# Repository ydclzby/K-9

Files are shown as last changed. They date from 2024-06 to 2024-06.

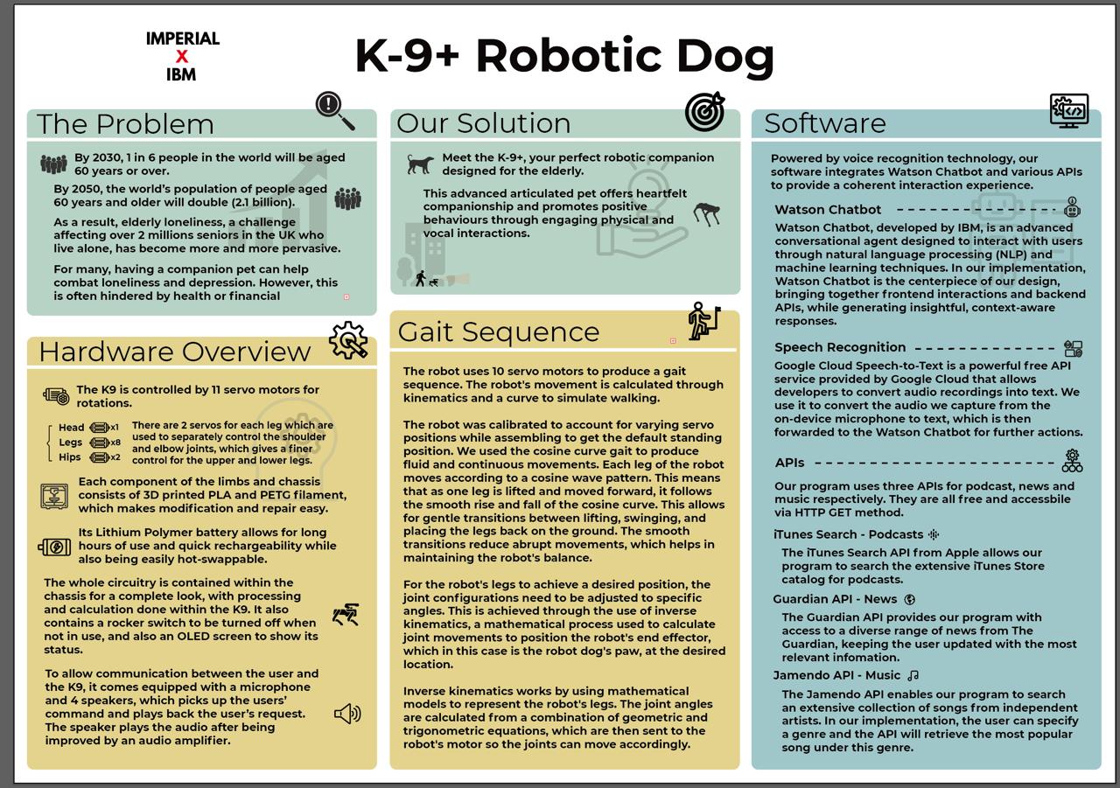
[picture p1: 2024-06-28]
Promotional Material/Poster K9.jpg

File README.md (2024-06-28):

# K-9+
Imperial team with IBM

Group Members:
- Krrish Jain
- William Ho
- Ryusei Kinosaki
- Chenglin Sun
- Boyan Zhang
- Qidong Zhou

## Introduction

The aim of this project was to build an AI companion robot pet for the elderly with the following features:

- Listen to voice commands to control the pet
- Control the movement of the pet
- Allow the pet to read the news
- Play music or podcasts requested by the user

These features help to encourage more positive behaviours for the user, through engaging physical and vocal interactions, as well as, providing companionship to help combat elderly loneliness.

### Project Manangement and Meetings

At the start of the project, there were multiple meetings to set up the necessary steps and schedule towards completion, and to give each team member a clear responsibility to contribute towards the project, which are shown [here](https://github.com/ydclzby/K-9/tree/main/Meeting%20Notes). After each part was completed and functional, it was integrated with other team member's work to create a subsystem. Each subsystem was then integrated together to create the K9, for which the team met almost every day.

## Hardware
### Components
The robodog consists of the following components:

* 11x MG995 Servo Motor
* 1x 6V, 5.5A Buck Voltage Converter
* 1x 6V to 5V/8A Buck Voltage Converter
* 1x 11.1V 3500mAh 3S1C Lithium Ion Battery
* 1x Adafruit Mini USB Microphone
* 1x MikroElektronika 2x20W Audio Amplifier
* 1x Raspberry Pi 4B (8GB RAM)
* 1x 16A Rocker Switch
* 1x OLED 128x64 Pixels
* 1x 300mm RPi Camera Ribbon
* 1x Raspberry Pi Camera
* 4x 8 Ω 1 W Speaker
* 4x Squash Balls
* PLA Filament
* PETG Filament
  
### CAD Design
The IBM K-9 bot's body is divided into 3 parts: the chassis, the legs and the head, where each of them were designed for the sake of practicality, manoeuverability and compactness.
Unless otherwise specified, the material used are PLA filament, which were 3D printed for the sake of rapid prototyping and bespoke modifications. The design was inspired by this [design](https://grabcad.com/library/quadruped-robot-w-code-1), which was shown to work consistently.

<h2>Legs</h2>
The mechanism of the legs is controlled by two servos, each controlling the shoulder (upper half of the leg) and the elbow (lower half of the leg).
The torque of the shoulder is controlled directly via the servo, whose circular attachment is slotted into the shoulder and fastened with a screw.
The torque of the elbow is transfered via the links which are attached between the servo and the elbow.
Finally, the feet of the chassis is a squash ball cut into half. The advantage of the squash ball is the higher friction surface and elasticity, preventing the K-9 from slipping while walking towards the user.

The mechanism works consistently, however, collisions and wear could loosen the joints, hence improvemets is possible with the use of ball bearings and adjusting the cad so the bearings would slot into them.

<h2>Head</h2>
The head works as a housing for the audio amplifier, speaker and the camera which could not be put into the circuit within the chassis. The design was made to be as compact as possible so that the weight would not affect the walking control. Moreover, it was made with the same design approach as the legs, where it can be easily put on the servo's circular bit.

<h2>Chassis</h2>
The chassis itself was made mainly to house the circuitry, while also holding switches and the OLED display. Instead of making one large chassis, it was divided into parts so that only one small part had to be printed in case of any problems. The central body of the chassis was made by PETG filament whose flexibility allowed for the components to be assembled easier.

### Circuitry
The circuit that controls the robodog is shown in the block diagram below. Although the battery is enough to power both the servos and the raspberry pi, when all 10 servos are used for the gait, more energy is necessary, hence requiring a power bank to power the pi. A more potent battery such as LiPo is necessary, but was not used due to budget and regulation constraints.

K9 Block

The servos were controlled by the Servo HAT to optimise space and ease of use. The raspberry cam was connected via the camera cable to the raspberry pi, and the microphone and amplifier were connected through USB and audio cable, respectively. Finally, the OLED was used to display the IP for secure shell connection.

## Software

### Chatbot

The chatbot implementation leverages IBM Watson Assistant, speech recognition, and various other APIs to provide interactive functionalities. This section details the important classes and aspects involved in the chatbot implementation.

#### SysState Class

The `SysState` class is central to managing the state of the system and coordinating interactions between the various components and APIs.

##### Initialization

- **`__init__(self, history_fp)`**
  - Initializes system state variables.
  - Sets up the IBM Watson Assistant API.
  - Configures the Picamera and servos for movement.
  - Instantiates a `Quadruped` object for controlling the robot.

##### Methods

- **chatbot_thread()**
  - Initializes the IBM Watson Assistant using the provided API key and service URL.
  - Manages a session with the Assistant, sending user commands and processing responses.
  - Adjusts the system mode based on the Assistant's responses.

- **audio_thread()**
  - Listens for audio commands using a microphone.
  - Converts speech to text using the `speech_recognition` library.
  - Sets the recognized text as a command for processing.

- **mode_thread()**
  - Executes actions based on the current mode, such as reading text, playing podcasts, fetching news, playing songs, and controlling the robot's movements.

#### IBM Watson Assistant Integration

The IBM Watson Assistant is used to interpret user commands and provide responses. 

##### Methods

- **chatbot_thread()**
  - **authenticator = IAMAuthenticator(api_key)**
    - Authenticates using the IBM Cloud API key.
  - **assistant = AssistantV2(version='2024-05-03', authenticator=authenticator)**
    - Initializes the Assistant with the specified version and authenticator.
  - **assistant.set_service_url(service_url)**
    - Sets the service URL for the Assistant.
  - **response = assistant.create_session(assistant_id=assistant_id).get_result()**
    - Creates a session with the Assistant.
  - **response = assistant.message(assistant_id=assistant_id, session_id=session_id, input=message_input).get_result()**
    - Sends user commands to the Assistant and processes the response.

#### Speech Recognition Integration

The `speech_recognition` library is used to capture and interpret audio commands from the user.

##### Methods

- **audio_thread()**
  - **recognizer = sr.Recognizer()**
    - Initializes the recognizer.
  - **mic = sr.Microphone()**
    - Sets up the microphone.
  - **audio = recognizer.listen(source, timeout=5.0, phrase_time_limit=3.0)**
    - Listens for audio input with a timeout and phrase time limit.
  - **recognized_text = recognizer.recognize_google(audio)**
    - Converts the captured audio to text using Google’s speech recognition API.

#### Additional APIs and Functionalities

##### News API

The News API fetches the latest news articles on a given topic.

- **get_news(topic)**
  - **params = {'api-key': news_api_key, 'q': topic, 'page-size': 1, 'order-by': 'relevance'}**
    - Sets the parameters for the news search.
  - **response = requests.get(news_endpoint, params=params)**
    - Sends a request to the News API to fetch articles.

##### iTunes API

The iTunes API is used to search for and play podcasts.

- **first_podcast(topic)**
  - **params = {'term': topic, 'media': 'podcast', 'limit': 1}**
    - Sets the parameters for the podcast search.
  - **response = requests.get(itunes_search_url, params=params)**
    - Sends a request to the iTunes API to search for podcasts.

##### Jamendo API

The Jamendo API fetches songs based on a given topic.

- **get_song(topic)**
  - **params = {'client_id': CLIENT_ID, 'format': 'json', 'limit': 1, 'tags': topic, 'order': 'popularity_total_desc'}**
    - Sets the parameters for the song search. This implementation fetches the most popular song under a user-specified genre (topic).
  - **response = requests.get(api_url, params=params)**
    - Sends a request to the Jamendo API to search for songs.

#### Thread Management

The chatbot employs threading to manage different tasks concurrently.

- **threading.Thread(target=ibm_Chatbot.chatbot_thread).start()**
  - Starts the chatbot thread to handle interactions with IBM Watson Assistant.
- **threading.Thread(target=ibm_Chatbot.audio_thread).start()**
  - Starts the audio thread to capture and process audio commands.
- **threading.Thread(target=ibm_Chatbot.mode_thread).start()**
  - Starts the mode thread to execute actions based on the system mode.

### Movement

For the movement, the quarduped_new.py file contains 2 classes which are responsible for controlling the robot's movements. Using the adafruit_servokit library to control the servos, the approach we chose to use was to use inverse kinematics to calculate where to position each leg.

#### Motor Class

The motor class is used to help identify the corresponding pin location with the motor location.

#### Quadruped Class

The quardruped class is the main class to control the robot. 

- The class constructor __init__, initialises the object and instantiates the ServoKit and defines the initial lengths and angles for the leg. It also sends out a pulse width range for each servo motor.
- There are 2 functions to assist with controlling the movement, set_angle, and rad_to_degree. These functions help by setting the angle for the servo and converting radians to degrees, respectively.
- The calibrate function sets the pet to it's standing up position by getting those values from a dictionary, pos_dict.
- The sit function sets the pet to a sitting position by getting the standing up position from the dictionary, pos_dict, and adjusting the shoulder values by a constant value.
- The inverse_kinematics functions runs to get the desired angles, theta1 and theta2, based on the target x and y co-ordinates.
- The move function will use the angle that is calculated in the inverse_kinematics function to set the angle of the servos to the desired positions, as well as being able to adjust the direction of movement.
- THe pushups function moves the robot to a calibrated position, lowers the back legs and then proceeds to lower and extend the front legs.
- The steps function will call on the move function based on direction for a certain number of steps.

For the inverse kinematics:
1. First calculate distance, d, as the square root of x squared + y squared
2. Then, calculate theta2, which is pi take away the arccos of the length of upper leg squared + lower leg squared - d squared divided by 2 times the lower leg length times the upper leg length.
3. Then, get phi, by getting the arccos of the upper leg squared - lower leg squared + d squared divided by 2 times the upper leg length times d squared.
4. Finally, theta1 is the arctan2 of y, x - phi.

### Computer Vision

The computer vision code is in the bone_detector.py file. This code contains one class, the Follower class, and is used to detect a green bone, the colour values are set in the variables colorLower and colorHigher. The code uses the picamera2 library for the camera and cv2 for computer vision. The code will capture array from the camera and turn it into HSV colour space which creates a mask based on the desired color ranges, noise is then removed from the mask and a moments is created of the binary mask. A rectangle is then created around the desired object and will rotate the camera to center the object and turn the robot and move towards it.

## Setup
To start up the K9, make sure that the battery is fully charged (~12.3V) and the rocker switch is set to on. Give a few minutes for the Pi to switch on, at which point the OLED at the back should show the IP when connected to the imperial network. With the K9 connected to the network, you can use your own laptop with a Linux command (Ubuntu command terminal on Windows/Mac works as well) to connect to the Pi with "sudo ssh K9@<IP>". After accepting any prompts from the terminal, you can activate the programme by running "sudo python3 chatbot_9.py", at which it can listen for commands to do whichever issues.

## Acknowledgements
We'd like to thank Jon McNamara, our company liaison, for giving us the resources and guidance with our projects. We'd also like to thank our project supervisor, Professor Pal Bikash for helping us with feedback on promotinal materials such as our leaflets.

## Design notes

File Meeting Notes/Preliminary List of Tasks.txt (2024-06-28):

- Parts list
- Order
- Software
    - Microphone
    - Chatbot API
    - Movement control
    - Face/display
    - Collision avoidance
- Hardware
    - RPi
    - Arduino
- Chassis
    - Modelling
    - 3d Print/Laser cut

## Milestone and its respective deadlines + content

1. Create subteams & organisation/roles (2nd - 7th May)
    1. Software
        1. API w/ chatbot
        2. API w/ news/music/podcast etc.
        3. Movement (Servos/Control)
        4. Computer vision
    2. Hardware
        1. Chassis
        2. Electronics
2. Create Parts list - TBD after meeting with supervisor (7th) - Deadline 10th May
3. Ordering parts - Plan to order everything by the 10th (Deliver within a week ideally)
4. Software
    1. Chatbot API with microphone on laptop (1 wk)
    2. Finding podcast & news API (1 wk)
    3. Computer vision with camera (2 wks)
5. Hardware
    1. Completing Chassis (27th May)
    2. Servo Config and control (27th May)
    3. Breadboard prototype circuit for additional sensors (20th May)
    - Possible delays from broken circuits/reprint chassis part
6. Integration (start 28th May  - 3rd June) 
    1. State machine/workflow of the bot (walking, playing music etc)
    2. Uploading different software parts on pi & debug [1 week]
    3. Movement + obstacle avoidance debugging with software/sensors [1.5 weeks]
    - In case of chassis delay - software team should start on the pi itself and integrating mic/speaker
7. Final Integration (start 13th June - 20th June)
    1. Test runs and final adjustments
    2. edge case if there is

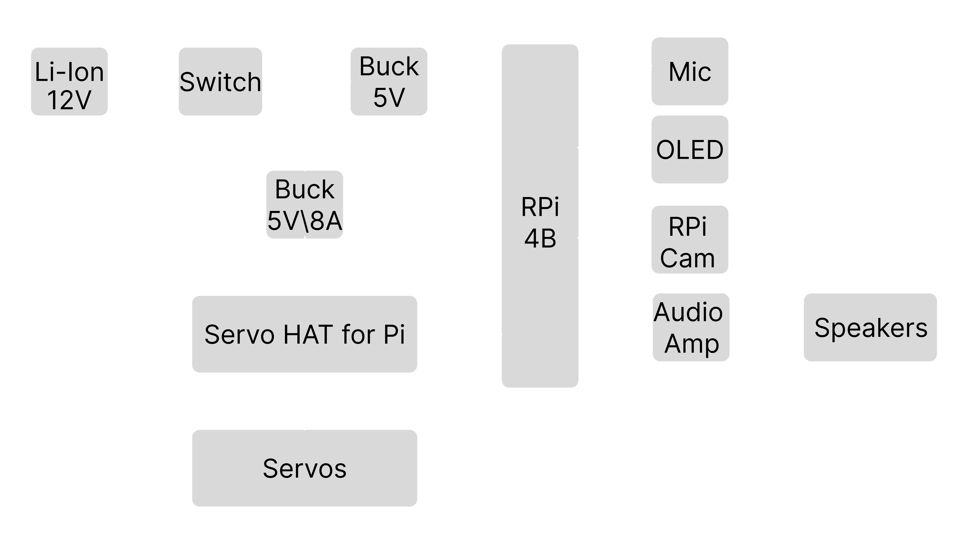
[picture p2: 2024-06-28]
images/K9 Block.png

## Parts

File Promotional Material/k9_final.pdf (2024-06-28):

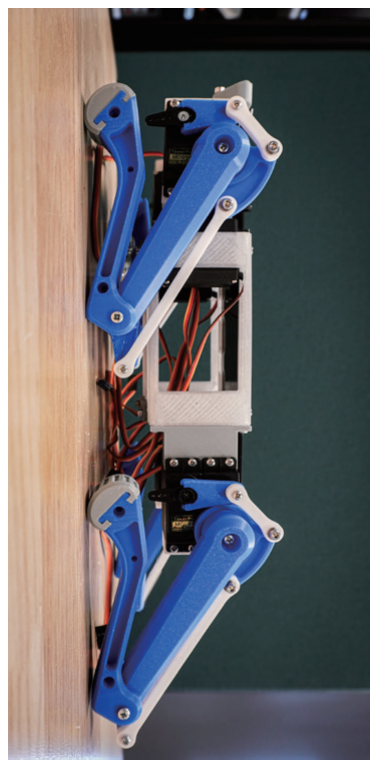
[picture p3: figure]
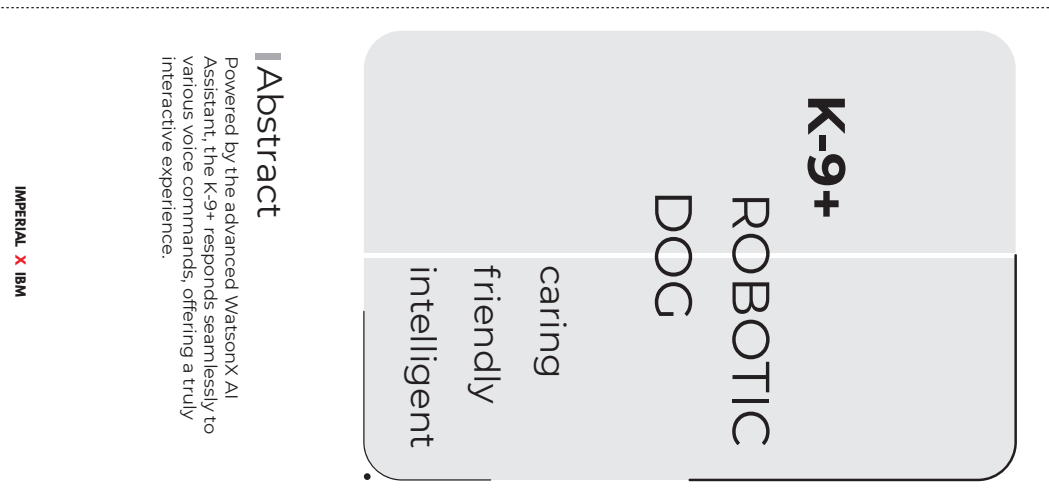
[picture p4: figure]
IMPERIAL IBM X; interactive experience.; Powered by the advanced WatsonX AI; Abstract; intelligent; friendly; caring; ROBOTIC; DOG

various voice commands, offering a truly

Assistant, the K-9+ responds seamlessly to

# Quadruped Design Hardware

navigate various terrains.

offers excellent stability, allowing it to easily

realistic movement. This advanced structure

10 degrees of freedom, enabling smooth and

The K-9+ features a quadruped design with you and motivate a healthier lifestyle.
software and computer vision, it can follow

raspberry pi running sophisticated control

natural interactions. Equipped with a

real dog, the K-9+ has lifelike movement and

# Inspired by the form and movement of a K-9+

RYUSEI KINOSAKI, QIDONG ZHOU & BOYAN ZHANG

KRRISH JAIN, WILLIAM HO, CHENGLIN SUN,

Designed by
We are a robotics technologies research

# About Us

https://github.com/ydclzby/ZMS_K9-

GitHub:

www.imperial.ac.uk

Website:

SW7 2BX

South Kensington

Imperial College London

Address:

# Contact Us

others and giving back to the society.

London Engineers with the aim of helping

group founded by six Imperial College

IMPERIAL IBM X IMPERIAL IBM X

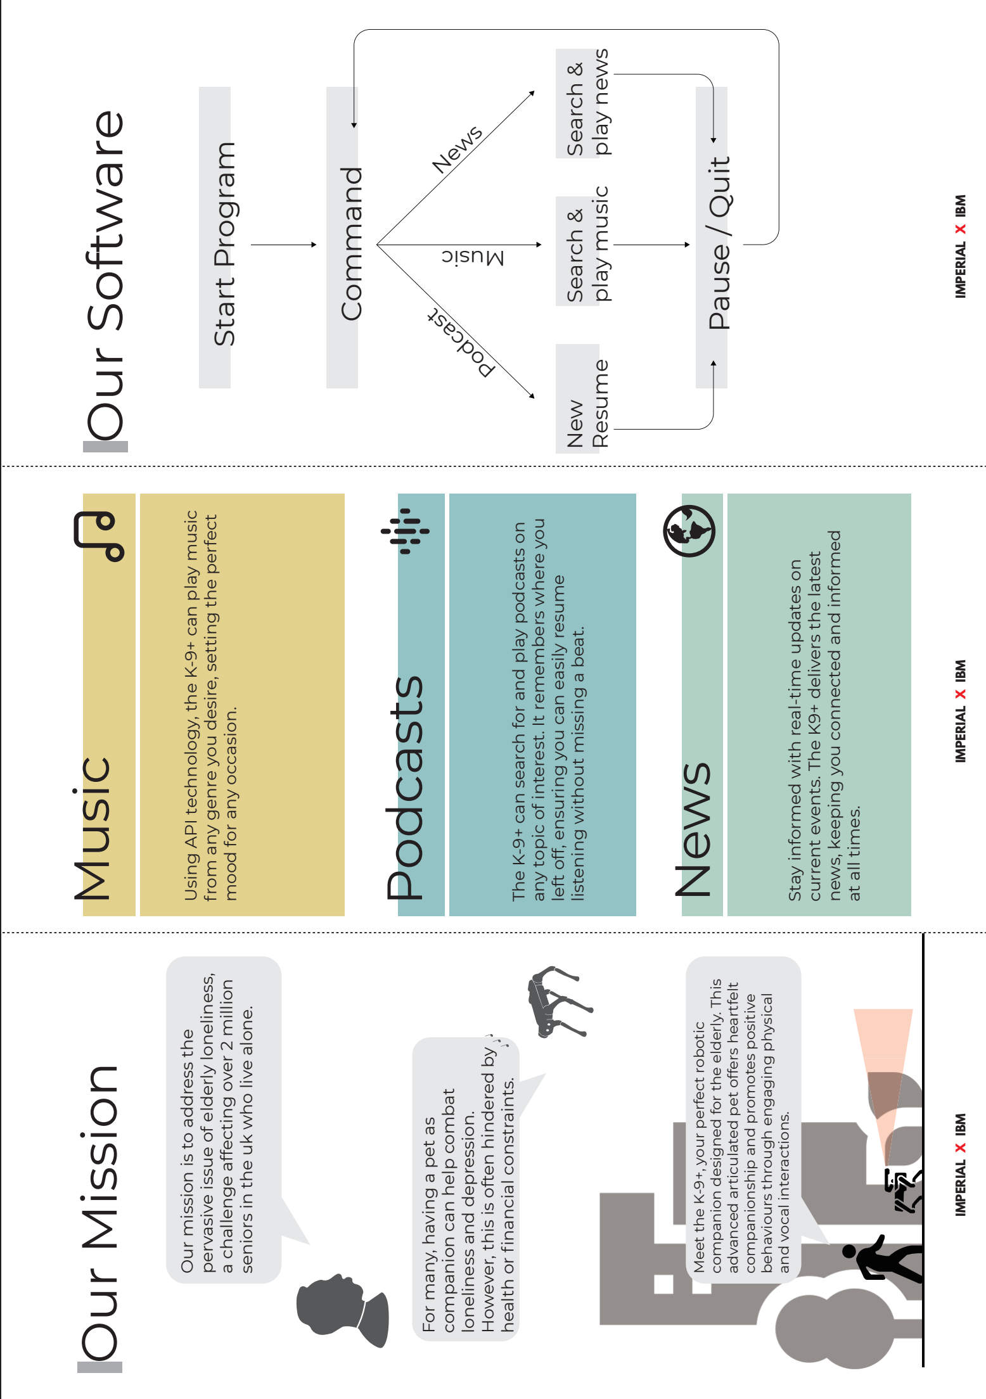
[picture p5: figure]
IMPERIAL IBM X; Our Mission Music; mood for any occasion.; Podcasts; listening without missing a beat.; News; Stay informed with real-time updates on; at all times.; Start Program; Command; Pause / Quit; New; Resume; Search &; play music; play news; Our mission is to address the; pervasive issue of elderly loneliness, a challenge affecting over 2 million seniors in the uk who live alone.; For many, having a pet as; companion can help combat loneliness and depression.; However, this is often hindered by health or financial constraints.; Meet the K-9+, your perfect robotic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

Using API technology, the K-9+ can play music
from any genre you desire, setting the perfect The K-9+ can search for and play podcasts on

any topic of interest. It remembers where you

left off, ensuring you can easily resume current events. The K9+ delivers the latest

news, keeping you connected and informed

companion designed for the elderly. This

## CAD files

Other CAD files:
CAD/Head v13.f3z
CAD/Quadruped_motor_extension_taller v3.f3d
CAD/Rear Block v12.f3d
CAD/link_belly v10.f3z

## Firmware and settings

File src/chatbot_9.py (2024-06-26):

import os 
from ibm_watson import AssistantV2
from ibm_cloud_sdk_core.get_authenticator import IAMAuthenticator
import speech_recognition as sr
import requests
import feedparser
from playsound import playsound
from urllib.parse import urlparse
from bs4 import BeautifulSoup



import threading
import vlc
import time
import json
import queue
from gtts import gTTS
from datetime import datetime
import numpy as np

# from gait_logic.quadruped import Quadruped


import cv2
from adafruit_servokit import ServoKit
from picamera2 import Picamera2
from time import sleep

from qudruped_new import Quadruped

itunes_search_url = "https://itunes.apple.com/search"

api_key = "c5fMtKdU7iDNdzmB0vIv9_t88rPExGfffuMxNCpqBQ1L"
service_url = "https://api.eu-gb.assistant.watson.cloud.ibm.com/instances/e5a41b2f-bd77-4e71-b02c-430b71625717"
assistant_id = "62222580-6d55-4e58-889f-515789eb2cd1"

news_api_key = "a0ff4132-cf60-48d7-b23f-d0523e7c67aa"
news_endpoint = "https://content.guardianapis.com/search"

threading_lock = threading.Lock()
podcast_lock = threading.Lock()
music_lock = threading.Lock()

podcast_history_fp = "../data/history/playback_history.json"

api_url = "https://api.jamendo.com/v3.0/tracks"

CLIENT_ID = 'cd92fac2'



class SysState(object):
    colorLower = (57, 100, 100)
    colorUpper = (77, 255, 255)

    HEAD_SERVO = 0
    tiltAngle = 90
    def __init__(self, history_fp):
        
        self.mode = None
        self.wait_command = True
        self.command_text = ""
        self.response = ""
        self.topic = ""
        self.control_command = "none"
        self.mic = True
        
        # Players
        self.history_fp = history_fp
        self.player = None
        self.current_start_time = None
        self.paused_arg = False
        self.quit_arg = False
        self.history_data = {}
        self.control_command = None
        self.found = True
        #self.r = Quadruped()
        
        # CV
        self.picam2 = Picamera2()
        self.picam2.configure(self.picam2.create_preview_configuration(main={"format": 'XRGB8888', "size": (640, 480)}))
        self.picam2.start()
        self.kit = ServoKit(channels=16)
        self.kit.servo[0].set_pulse_width_range(500,2500)
        self.set_servo_angle(90)
        self.tiltAngle = 90
        self.cv_switch = True
        self.centred = False
        self.r = Quadruped()
        self.r.calibrate()
        
    def set_servo_angle(self,degrees):
        self.kit.servo[0].angle = degrees

    def move_servo(self,x,y):
        if (x < 240):
            self.tiltAngle += 3
            if self.tiltAngle > 140:
                self.tiltAngle = 140
                #print("move left")
            self.set_servo_angle (self.tiltAngle)
            sleep(0.02)
        if (x > 400):
            self.tiltAngle -= 3
            if self.tiltAngle < 40:
                self.tiltAngle = 40
                #print("move right")
            self.set_servo_angle (self.tiltAngle)
            sleep(0.02)
            
    def start_follow(self):
        
        while True:
            
            im = self.picam2.capture_array()
            hsv = cv2.cvtColor(im, cv2.COLOR_BGR2HSV)

            mask = cv2.inRange(hsv, self.colorLower, self.colorUpper)
            mask = cv2.erode(mask, None, iterations=2)
            mask = cv2.dilate(mask, None, iterations=2)

            M = cv2.moments(mask)

            centre_x = -1
            centre_y = -1

            if M["m00"] > 0:
                cx = int(M["m10"] / M["m00"])
                cy = int(M["m01"] / M["m00"])

                x, y, w, h = cv2.boundingRect(mask)
                cv2.rectangle(im, (x, y), (x + w, y + h), (0, 0, 255), 2)
                centre_x = x + w/2
                centre_y = y + y/2
                #print("(x,y) = ({0},{1})".format(centre_x,centre_y))
            else:
                centre_x = -1
                centre_y = -1

            if (centre_x != -1 and centre_y != -1):
                self.move_servo(centre_x, centre_y)
                if(self.centred):
                    self.move_bot(x,y,w,h)

            #cv2.imshow("Frame", im)
            key = cv2.waitKey(1) & 0xFF
            if key == ord("q"):
                break
            
            if self.cv_switch == False:
                break
            
        
        cv2.destroyAllWindows()
        
    def read_podcast_history(self):
        try:
            with open(self.history_fp, "r") as file:
                self.history_data = json.load(file)
        except FileNotFoundError:
            print(f"No history file found at {self.history_fp}.")
            self.history_data = None
            
    def save_padcast_history(self):
        with open(self.history_fp, "w") as file:
            json.dump(self.history_data, file, indent=4)  # Save only a single episode
        print(f"Playback history saved to {self.history_fp}")
        
    def first_podcast(self, topic):
        
        params = {
            "term": topic,
            "media": "podcast",
            "limit": 1
        }
        
        response = requests.get(itunes_search_url, params=params)
        
        if response.status_code == 200:
            
            data = response.json()
            results = data.get("results", [])

            if results:
                feed_url = results[0].get("feedUrl")
                print(f"Podcast RSS Feed: {feed_url}")

                feed = feedparser.parse(feed_url)

                if feed.entries:
                    
                    first_episode_url = feed.entries[0].enclosures[0].href
                    episode_title = feed.entries[0].title
                    print(f"First Episode Title: {episode_title}")
                    print(f"First Episode URL: {first_episode_url}")

                    instance = vlc.Instance()
                    self.player = instance.media_player_new()
                    media = instance.media_new(first_episode_url)

                    self.player.set_media(media)
                    self.player.audio_set_volume(100)  # Adjust volume
                    print("Streaming the first episode...")
                    self.player.play()

                    # Record the start time and add a record to the history
                    self.current_start_time = time.time()
                    history_entry = {
                        "title": episode_title,
                        "url": first_episode_url,
                        "duration_listened": 0  # Initialize with zero; updated when stopping
                    }
                    self.history_data = history_entry  # Replace existing entries with the new one
                    self.podcast_control()
            else:
                self.found = False
        else:
            print(f"Error fetching data: {response.status_code}")
    
    def podcast_control(self):
        while True:
            # command = self.control_command
            if self.control_command == None:
                pass  
            
            if self.control_command == "follow me":
                self.tracking()
                #self.control_command = None
            if self.control_command == "sit down":
                self.sit()
                #self.control_command = None
                
            if self.control_command == "stop" and self.player and not self.paused_arg:
                print("Pausing playback...")
                self.player.pause()
                self.paused_arg = True
                if self.current_start_time is not None:
                    elapsed_time = time.time() - self.current_start_time
                    self.history_data["duration_listened"] += elapsed_time
                #self.control_command = None
            if self.control_command == "resume" and self.player and self.paused_arg:
                print("Resuming playback...")
                self.player.play()
                self.paused_arg = False
                self.current_start_time = time.time()
                #self.control_command = None
            if self.control_command == "quit":
                print("Quitting playback and updating history...")
                self.quit_arg = True
                if self.player:
                    self.player.stop()
                # Update the final duration listened
                if self.current_start_time is not None:
                    elapsed_time = time.time() - self.current_start_time
                    self.history_data["duration_listened"] += elapsed_time
                self.save_padcast_history()
                self.control_command = None
                break
            self.control_command = None
            
            
         
    def play_history(self):
        self.read_podcast_history()
        if not self.history_data:
            return
        
        url = self.history_data["url"]
        duration_listened = self.history_data["duration_listened"]
        print(f"Resuming '{self.history_data['title']}' from {duration_listened} seconds...")
        
        instance = vlc.Instance()
        self.player = instance.media_player_new()
        media = instance.media_new(url)
        
        self.player.set_media(media)
        self.player.audio_set_volume(100)  # Adjust volume
        self.player.play()
        
        while self.player.get_state() not in (vlc.State.Playing, vlc.State.Paused):
            time.sleep(0.1)
        self.player.set_time(int(duration_listened * 1000))

        self.paused_arg = False
        self.current_start_time = time.time()
        self.podcast_control()
                   
    def get_news(self, topic):
        #get news url
        quit = False
        params = {
            'api-key': news_api_key,
            'q': topic,  # Search term, can be customized
            'page-size': 1,  # Number of results per page
            'order-by': 'relevance',  # or relevance
        }

        response = requests.get(news_endpoint, params=params)

        if response.status_code == 200:
            data = response.json()
            articles = data.get('response', {}).get('results', [])

            for article in articles:
                news_title = article.get('webTitle', 'No title')
                news_url = article.get('webUrl', '#')
                print(f"Title: {news_title}")
                print(f"URL: {news_url}")
                print()
        else:
            print("Failed to fetch content. HTTP status code:", response.status_code)
        
        #get news content
        response = requests.get(news_url)

        if response.status_code == 200:
            #clear the original txt file
            with open("../data/news_content.txt", 'w') as file:
                pass

            # Parse the HTML content
            soup = BeautifulSoup(response.text, 'html.parser')

            # Extract relevant parts of the article (e.g., the headline and content)
            headline = soup.find('h1')  # Assuming the headline is in an <h1> tag
            paragraphs = soup.find_all('p')  # Extract all paragraph content

            # Display the headline
            if headline:
                print(f"Headline: {headline.get_text()}")
            player = vlc.MediaPlayer()
            # Display the content of the article
            for p in paragraphs:
                if not quit:
                    with open("../data/news_content.txt", 'a') as file:
                        file.write('\n' + p.get_text())
                    print(p.get_text())
                    tts = gTTS(text=p.get_text(), lang='en')
                    tts_file = "temp_speech.mp3"
                    tts.save(tts_file)
                    self.player = None
                    media = vlc.Media(tts_file)
                    instance = vlc.Instance()
                    self.player = instance.media_player_new()
                    self.player.set_media(media)
                    self.player.play()
                    
                    while self.player.is_playing():
                        if self.control_command == "quit":
                            quit = True
                            self.player.stop()
                            self.player = None
                            self.control_command = None
                            break
                    os.remove(tts_file)
        else:
            print('Failed to fetch the article content. Status Code:', response.status_code)

    def read_text(self, text_to_speak):
        tts = gTTS(text=text_to_speak, lang='en')
    
        # Save the speech as a temporary file
        tts_file = "temp_speech.mp3"
        tts.save(tts_file)
        
        # Play the speech using playsound
        playsound(tts_file)
        
        # Delete the temporary file
        os.remove(tts_file)

    def get_song(self, topic):
        params = {
            'client_id': CLIENT_ID,
            'format': 'json',
            'limit': 1,  # Get only the top result
            'tags': topic,
            'order': 'popularity_total_desc'
        }
        
        try:
            response = requests.get(api_url, params=params)
            response.raise_for_status()  # Raises an exception for HTTP error responses
            
            # Parse the JSON response
            data = response.json()
            
            # Check if any tracks were found
            if data['headers']['status'] == 'success' and data['results']:
                track = data['results'][0]
                # return track['name'], track['artist_name'], track['audio']
                instance = vlc.Instance()
                self.player = instance.media_player_new()
                media = instance.media_new(track['audio'])
                
                self.player.set_media(media)
                self.player.audio_set_volume(100)
                print("Streaming music")
                self.player.play()
                self.music_control()
            else:
                self.found = False
                
        except requests.RequestException as e:
            return f"An error occurred: {str(e)}", None, None
        
    def music_control(self):
        while True:
            # command = self.control_command
            if self.control_command == None:
                pass 
            
            if self.control_command == "follow me":
                self.tracking()
                #self.control_command = None
            if self.control_command == "sit down":
                self.sit()
                #self.control_command = None
                
            if self.control_command == "stop" and self.player and not self.paused_arg:
                print("Pausing the song...")
                self.player.pause()
                self.paused_arg = True
                #self.control_command = None

            if self.control_command == "resume" and self.player and self.paused_arg:
                print("Resuming playback...")
                self.player.play()
                self.paused_arg = False
                #self.control_command = None

            if self.control_command == "quit":
                print("Quitting the song...")
                self.quit_arg = True
                if self.player:
                    self.player.stop()
                self.control_command = None
                break
            self.control_command = None
         
    def move_bot(self,x,y,w,h):
        if(self.tiltAngle < 80):
            print("move right")
            self.r.move(0, 1.5, 2)
        #turn right

        elif(self.tiltAngle > 100):
            print("move left")
            self.r.move(0, 1.5, 3)
        #turn left

        else:
            print("move forward")
            area = w * h
            print("Area = {}".format(area))
            self.r.move(2, 3, 0)
        #forward

    def set_servo_angle(self,degrees):
        self.kit.servo[0].angle = degrees

    def move_servo(self,x,y):
        if (x < 260):
            self.centred = False
            self.tiltAngle += 1
            if self.tiltAngle > 140:
                self.tiltAngle = 140
            #print("move left")
            self.set_servo_angle (self.tiltAngle)
            sleep(0.02)
        elif (x > 380):
            self.centred = False
            self.tiltAngle -= 1
            if self.tiltAngle < 40:
                self.tiltAngle = 40
            #print("move right")
            self.set_servo_angle (self.tiltAngle)
        else:
            self.centred = True
            sleep(0.02)   
            
        
    def tracking(self):
        self.start_follow()
        
    def sit(self):
        self.r.sit()
        
    def stand(self):
        self.r.calibrate()
        
    def pushup(self):
        self.r.pushups()
    
    def chatbot_thread(self):
        # Set up the authenticator and assistant
        authenticator = IAMAuthenticator(api_key)
        assistant = AssistantV2(
            version='2024-05-03',  # Use the correct version date
            authenticator=authenticator
        )
        assistant.set_service_url(service_url)

        # Create a new session
        try:
            response = assistant.create_session(assistant_id=assistant_id).get_result()
            session_id = response['session_id']

            while True:
                if(self.found == False):
                    self.command_text = 'not found'
                    
                if(self.wait_command == False or self.found == False ):
                    
                    print("-----------------------------------------------")
                    print("user input is:", self.command_text)
                    # Send a message to the chatbot

                    message_input = {
                        'message_type': 'text',
                        'text': self.command_text
                    }

                    response = assistant.message(
                        assistant_id=assistant_id,
                        session_id=session_id,
                        input=message_input
                    ).get_result()

                    # Print the chatbot's response
                    if response['output']['generic']:
                        self.response = response['output']['generic'][0]['text']
                        response_label = response['output']['generic'][-1]['text'][1]
                        response_content = ""
                        for message in response['output']['generic']:
                            response_content += message['text'][5:]

                        #print("Assistant:", response['output']['generic'][0]['text'])
                        if response_label == '0': #unknown commands
                            print("unknown command")
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

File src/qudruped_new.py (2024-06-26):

from adafruit_servokit import ServoKit
from enum import IntEnum
import math
import bezier
import numpy as np
from time import sleep


#from measurements
#FR:
# shoulder angle: 138
# elbow angle: 75
class Motor(IntEnum):
    # identifies the corresponding pin location with the motor location
    FR_SHOULDER = 4
    FR_ELBOW = 2
    FR_HIP = 9
    FL_SHOULDER = 3
    FL_ELBOW = 1
    FL_HIP = 10
    BR_SHOULDER = 6
    BR_ELBOW = 8
    BL_SHOULDER = 5
    BL_ELBOW = 7

class Quadruped:

    #    pos_dict = {Motor.FR_SHOULDER: 87, Motor.FR_ELBOW: 58, Motor.FR_HIP:95, Motor.FL_SHOULDER: 90, Motor.FL_ELBOW:94, Motor.FL_HIP:75, Motor.BR_SHOULDER:73, Motor.BR_ELBOW:62, Motor.BL_SHOULDER:86, Motor.BL_ELBOW:90}
#    pos_dict = {Motor.FR_SHOULDER: 70, Motor.FR_ELBOW: 47, Motor.FR_HIP:90, Motor.FL_SHOULDER: 106, Motor.FL_ELBOW:96, Motor.FL_HIP:83, Motor.BR_SHOULDER:63, Motor.BR_ELBOW:65, Motor.BL_SHOULDER:100, Motor.BL_ELBOW:84}
    pos_dict = {Motor.FR_SHOULDER: 65, Motor.FR_ELBOW: 62, Motor.FR_HIP:90, Motor.FL_SHOULDER: 106, Motor.FL_ELBOW:81, Motor.FL_HIP:83, Motor.BR_SHOULDER:60, Motor.BR_ELBOW:80, Motor.BL_SHOULDER:100, Motor.BL_ELBOW:69}
    shoulder_ang_measured = 138
    elbow_ang_measured = 75

    L1 = 10  # Upper leg length in cm
    L2 = 10.5  # Lower leg length in cm
    def __init__(self):
        self.kit = ServoKit(channels=16)
        self.upper_leg_length = 10
        self.lower_leg_length = 10.5
        for i in range(10):
            self.kit.servo[i].set_pulse_width_range(500,2500)
            sleep(0.2)

        #from measurements FR shoulder angle is 360-138 and elbow angle is 180-75
        initial_shoulder_angle = np.radians(360-self.shoulder_ang_measured)
        initial_elbow_angle = np.radians(180-self.elbow_ang_measured)
        shoulder_x, shoulder_y = 0, 0
        elbow_x = self.L1 * np.cos(initial_shoulder_angle)
        elbow_y = self.L1 * np.sin(initial_shoulder_angle)
        self.initial_foot_x = elbow_x + self.L2 * np.cos(initial_shoulder_angle + initial_elbow_angle)
        self.initial_foot_y = elbow_y + self.L2 * np.sin(initial_shoulder_angle + initial_elbow_angle)



    def set_angle(self,motor_id, degrees):
        """
        set the angle of a specific motor to a given angle
        :param motor_id: the motor id
        :param degrees: the angle to put the motor to
        :returns: void
        """
        self.kit.servo[motor_id].angle = degrees

    def rad_to_degree(self,rad):
        """
        Converts radians to degrees
        :param rad: radians
        :returns: the corresponding degrees as a float
        """
        return rad*180/math.pi

    def calibrate(self):
        """
        sets the robot into the default "middle position" use this for attaching legs in right location
        :returns: void
        
        OLD CODE:
        self.set_angle(Motor.FR_SHOULDER, 87) #60 27 
        self.set_angle(Motor.FR_ELBOW, 58) # 85 27
        self.set_angle(Motor.FR_HIP, 95)
#        sleep(0.5)
        self.set_angle(Motor.FL_SHOULDER, 90) #117
        self.set_angle(Motor.FL_ELBOW, 94) #67
        self.set_angle(Motor.FL_HIP, 75)
        #sleep(0.5)
        self.set_angle(Motor.BR_SHOULDER, 73) #46
        self.set_angle(Motor.BR_ELBOW, 62) #89
        #sleep(0.5)
        self.set_angle(Motor.BL_SHOULDER, 86) #113
        self.set_angle(Motor.BL_ELBOW, 90) #87
        """
        self.set_angle(Motor.FR_SHOULDER, self.pos_dict[Motor.FR_SHOULDER]) #60 27 
        self.set_angle(Motor.FR_ELBOW, self.pos_dict[Motor.FR_ELBOW]) # 85 27
        self.set_angle(Motor.FR_HIP, self.pos_dict[Motor.FR_HIP])
        #sleep(0.5)
        self.set_angle(Motor.FL_SHOULDER, self.pos_dict[Motor.FL_SHOULDER]) #117
        self.set_angle(Motor.FL_ELBOW, self.pos_dict[Motor.FL_ELBOW]) #67
        self.set_angle(Motor.FL_HIP, self.pos_dict[Motor.FL_HIP])
        sleep(0.1)
        self.set_angle(Motor.BR_SHOULDER, self.pos_dict[Motor.BR_SHOULDER]) #46
        self.set_angle(Motor.BR_ELBOW, self.pos_dict[Motor.BR_ELBOW]) #89
        #sleep(0.5)
        self.set_angle(Motor.BL_SHOULDER, self.pos_dict[Motor.BL_SHOULDER]) #113
        self.set_angle(Motor.BL_ELBOW, self.pos_dict[Motor.BL_ELBOW]) #87


    def sit(self):
            
        self.set_angle(Motor.BR_SHOULDER, self.pos_dict[Motor.BR_SHOULDER]- 40) #46
        self.set_angle(Motor.BR_ELBOW, self.pos_dict[Motor.BR_ELBOW]) #89
        #sleep(0.5)
        self.set_angle(Motor.BL_SHOULDER, self.pos_dict[Motor.BL_SHOULDER] + 40) #113
        self.set_angle(Motor.BL_ELBOW, self.pos_dict[Motor.BL_ELBOW]) #87

        sleep(0.5)

        self.set_angle(Motor.FR_SHOULDER, self.pos_dict[Motor.FR_SHOULDER] - 10) #60 27 
        self.set_angle(Motor.FR_ELBOW, self.pos_dict[Motor.FR_ELBOW]) # 85 27
        self.set_angle(Motor.FR_HIP, self.pos_dict[Motor.FR_HIP])
        #sleep(0.5)
        self.set_angle(Motor.FL_SHOULDER, self.pos_dict[Motor.FL_SHOULDER] + 10) #117
        self.set_angle(Motor.FL_ELBOW, self.pos_dict[Motor.FL_ELBOW]) #67
        self.set_angle(Motor.FL_HIP, self.pos_dict[Motor.FL_HIP])
    
    
    def inverse_kinematics(self, shoulder_num, elbow_num, hip_num, x, y, z, right):
        d = np.sqrt(x**2 + y**2)
        #print(d)
        if d > (self.L1 + self.L2) or d < abs(self.L1 - self.L2):
            return None, None  # The target is unreachable
        theta2 = np.radians(180)-np.arccos((self.L1**2 + self.L2**2 - d**2) / (2 * self.L1 * self.L2))
        phi = np.arccos((self.L1**2 + d**2 - self.L2**2) / (2 * self.L1 * d))
        theta1 = np.arctan2(y, x) - phi
        #print((np.degrees(theta1),np.degrees(theta2),np.degrees(phi)))

        
        ch_right = 1
        if not right:
            ch_right = -1
        shoulder_servo_angle = self.pos_dict[shoulder_num] - ((np.degrees(theta1) + self.shoulder_ang_measured) * ch_right)
        elbow_servo_angle = self.pos_dict[elbow_num] + (((180-np.degrees(theta2)) - self.elbow_ang_measured) * ch_right)

        self.set_angle(shoulder_num, shoulder_servo_angle)
        self.set_angle(elbow_num, elbow_servo_angle)
        if(hip_num != None):
            hip_servo_angle = self.pos_dict[hip_num] + z.item() + 90
            #print(z)
            #print(hip_servo_angle)

            self.set_angle(hip_num, hip_servo_angle)
            #print(np.degrees(z))
        #print((shoulder_servo_angle, elbow_servo_angle))

        return theta1, theta2
    
    def move(self, radiusX, radiusY, direction):

        arr_len = 60
        arr_len_half = arr_len/2
        t = np.linspace(0, 2 * np.pi, arr_len)

        #no phase change
        center_x = self.initial_foot_x + radiusX #change to + for other leg
        center_y = self.initial_foot_y

        foot_x = center_x - radiusX * np.cos(t) # change to - for other leg
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
